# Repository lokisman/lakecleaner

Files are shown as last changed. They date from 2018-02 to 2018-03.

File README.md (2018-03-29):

# Lake-Cleaner Bot

* Design of a Lake-Cleaner Bot.

====================================================================================

## Aim of project:
* The main task of this project is to clean the polluted water bodies with the help of a cleaning bot which is controlled wirelessly and can be made autonomous.
* The bot has to perform the functions of collecting the solid trash present in the water bodies like plastic bags, plastic bottles, small objects, etc. Further it should also be able to cut small plants and weeds growing on the water surface and also collect them in the trash pit. After this process, it should empty this trash into a disposable pit.

## CAD View
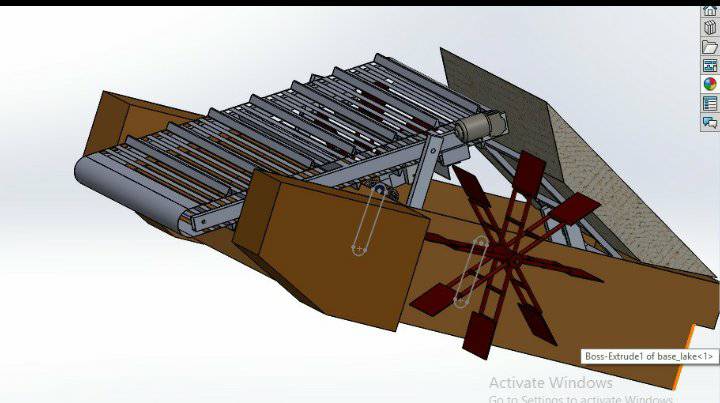
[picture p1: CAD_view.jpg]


====================================================================================

## Working principle:

### Conveyar mechanism
* This mechanism use for transfer waste,garbage from water body to dump box. The conveyer belt is mounted at an inclination to the chassis. As the cylinders over which the conveyer belt slides roll, the belt moves in the anti- clockwise direction so that the solid waste gets stuck in the projections made in the conveyer belt.

### Dumper Lifting Mechanism:
* It is use to lifting the box.
* In this lead screw mechanism is use. It gives us linear motion.
* Here, lead screw is mount on coupler.
* lead screw is mounted with motor shaft. So, when motor shaft is moved in anti-clockwise direction, due to linear motion dump box is move upward.

====================================================================================

## Different Parts:

### Chasis:       
* The chassis is designed so as to accommodate the wheels mountings, conveyer belt mechanism mounting, four link                            mechanism mounting and finally the chassis should sustain the weight of the (garbage + self-weight).

=====================================================================================

## Original Picture of Bot

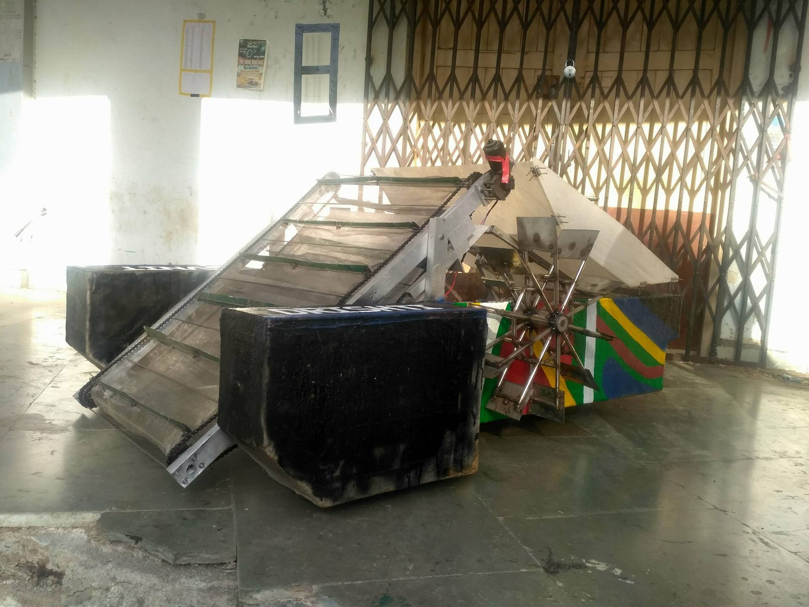
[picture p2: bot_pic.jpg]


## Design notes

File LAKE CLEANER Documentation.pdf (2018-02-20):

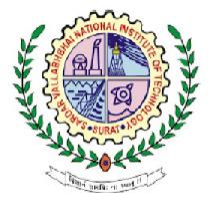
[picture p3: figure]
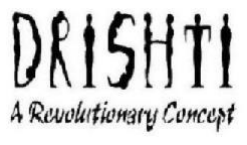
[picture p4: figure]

# _________________________ LAKE CLEANER

Project timeline spanned from 10th September,2017 to 15th February,2018
Team Members: | Mentors:
- | Parth Patel | Harshit Aghera
- Darshit Bhankar | Divya Poddar
- Darshan Wankhede | Sanjana Dhiran
- Lokesh Kumar Meena | Aparna Koduri
- Ranjeet Singh | Ankit Anand
- Yash Sharma | Kaishavi U.

# CONTENTS

1. Aim
2. Motivation
3. Working Mechanisms
a. Trash Collecting Mechanisms
b. Dumper Lifting Mechanisms
c. Chassis
d. Weed Cutting Mechanisms
4. Manufacturing
a. Chassis
b. Lead Screws
c. Wheels
d. Conveyer Belt
e. Body
f. Cutting Mechanism
5. Future Modifications
6. Result

# AIM OF THE PROJECT:

The main aim of the project is to clean the polluting water bodies with the help of a cleaning bot which is controlled wirelessly and further can be made autonomous.

The bot has to perform the functions of collecting the solid trash present in the water bodies like plastic bags,plastic bottles,small objects,etc… Further it should also be able to cut the small plants and weeds growing on the water surface and also collect them in the trash pit. After this process, it should empty this trash into a disposable pit.

# MOTIVATION:

Nowadays, a lot of manual labour is being is employed in the cleaning of the rivers, lake and other local water bodies. A large amount of time and money is wasted by the government in this task to reduce the river contamination.

Hence to provide a Technical Solution for a Time and Cost Effective method to reduce the manual labour, we thought of making an automatic bot which can efficiently do all the chores in less time. This is the basic motive behind our “River Cleaning Bot”.

## DESIGNING SOFTWARE USED:

## SolidWorks

## ANALYSIS SOFTWARE USED:

## Ansys

# WORKING PRINCIPLE:

The different mechanisms used in the different parts of the bot are as follows:

(A) Trash Collection Mechanisms:
(i) PNEUMATICS:
Pneumatics is a type of linear actuator which uses air pressure as the actuating force.
We thought of using the pneumatics to lift the collecting plates to a certain level and we would use four link mechanism to lift this whole assembly to dump this collected trash in our dumper container.
We made a SolidWorks Model for our mechanism and manufactured it.

Errors in the Mechanism:

1) The air pressure was not able to bear enough weight. Appropriate amount of the air pressure required was not being generated in the cylinders. This reduced the amount of garbage that the bot can carry at a time.
2) The air pressure in the cylinder would reduce at a faster rate. So while in operation, the cylinders will have to be refilled many times in quick succession. This will increase the cost of operation and also it is not feasible to again and again fill the cylinders.
3) We would have to install a pressure regulator to maintain the air pressure at a constant value.
So, we had to switch over to some other alternative mechanism.

(ii) CONVEYER BELT MECHANISM: This mechanism uses a Conveyer belt to collect the solid waste from the water body and transfer it to our dumper container. The conveyer belt is mounted at an inclination to the chassis. As the cylinders over which the conveyer belt slides roll, the belt moves in the anti- clockwise direction so that the solid waste gets stuck in the projections made in the conveyer belt. Just below the conveyer belt assembly is kept our dumper container. When the dumper is full, our four link mechanism lifts this dumper and disposes off trash out of the bot on the ground.

(B)Dumper Lifting Mechanisms:
(i) FOUR LINK MECHANISM:
We thought of various designs by the help of which we can lift the dumper upto such an elevation so that the trash can fall on the ground without any trash being left inside the dumper.

Our main aim was to give minimum rotation to the driver link and get maximum inclination of the dumper.

We finally arrived at the above design. Here the Inclination we get is the maximum.

(ii) LEAD SCREW MECHANISM: We are using a lead screw arrangement for the lifting of the dumper. The lead screw arrangement works as a linear actuator in our case. We mount the lead screw onto the chassis of the bot. The nut traverses on the lead screw and pushes the dumper along with it. So basically, there is one fixed link, two movable links and a lead screw. This completes our mechanism for the lifting of dumper container.

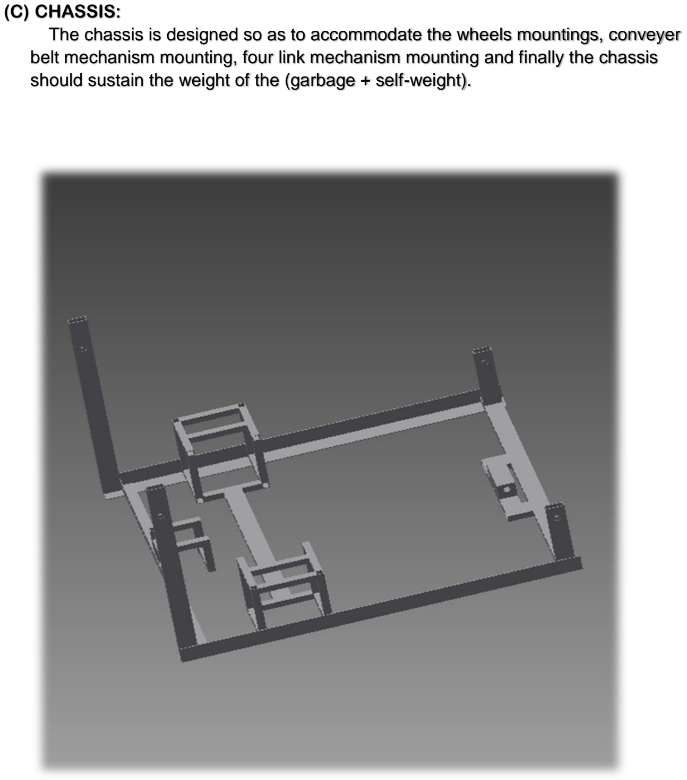
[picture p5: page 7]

(C) CHASSIS:
The chassis is designed so as to accommodate the wheels mountings, conveyer belt mechanism mounting, four link mechanism mounting and finally the chassis should sustain the weight of the (garbage + self-weight).

(D) WEED CUTTING MECHANISM:
We thought about two types of cutting/ shearing mechanisms which are :
(i) Reciprocating Type Cutter

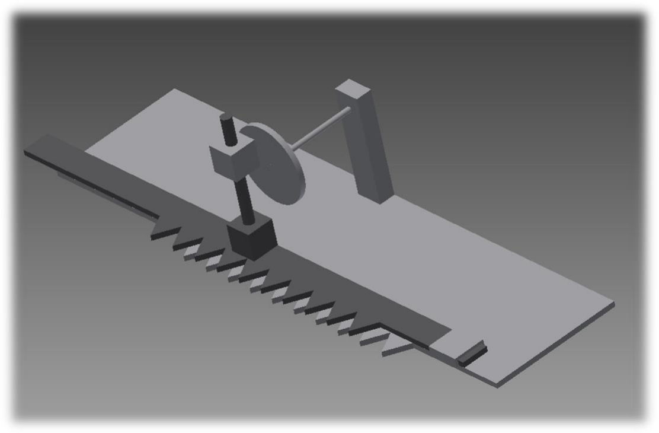
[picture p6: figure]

(ii) | Rotating Type Cutter
| In which the cutter roates and cuts the plants. The whole assembly is mounted on the arm which will have three degrees of freedom. By use of the arm we can adjust the depth of the cutter inside the water so that the cutting can be done at different depth.

# CAD DESIGNS:

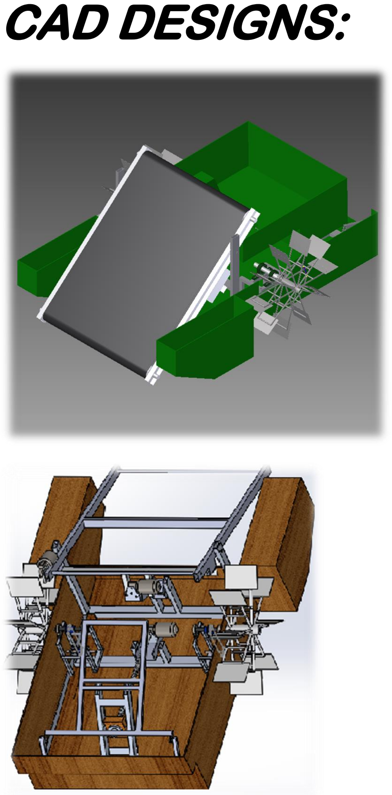
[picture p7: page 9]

# MANUFACTURING:

## Materials Used:

- Aluminium Sheets, Aluminium Box Sections
- Teak Wood
- Plywood
- FRP(For Body)
- Stainless Steel(For Propellers)

## Motors Used:

- Viper Motors (100 kgcm , 50 rpm)

## CHASSIS:

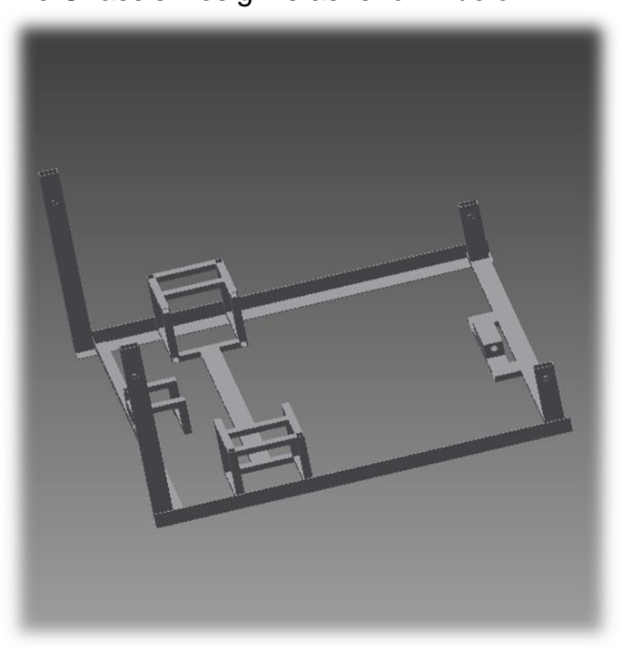
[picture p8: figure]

The Chassis Design is as shown below:

## LEAD SCREWS:

The motor mountings for the Lead Screws were manufactured with aluminium. Two of these were made. One for the garbage dumper and other for the adjustment of the inclination of the conveyer belt in the water.
The pillars for the hinging of the lead screw were also made and fixed exactly at the center of the middle link.

The problems faced with this was that:-
- The lead screw was wobbling very much even after properly connecting the coupler. We made the whole motor mounting twice but still the lead screw was wobbling about its axis. Due to this, the lead screw could not properly propagate on the nut and whole assembly was encountering jerks again and again. After checking each and every component in the mounting, we finally found that the coupler was not perfect. The holes which were connecting the lead screw with the coupler were not straight. Hence we made new holes and thus the problem was solved.
- The holes in the two pillars for hinging had to be exactly co-axial.

- The extension of the lead screw was hitting the bot as it was progressing further. Also the height of hinging was decided on the factor that the extension of the screw should not hit the bot. We had to cut some portion of the screw to reduce its length.

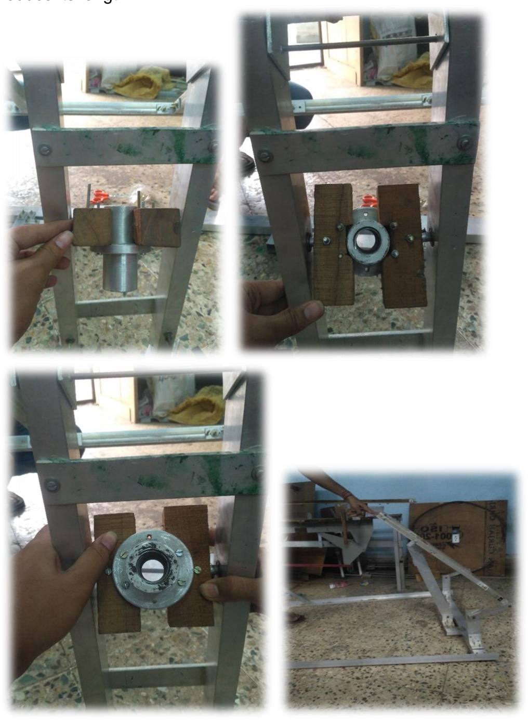
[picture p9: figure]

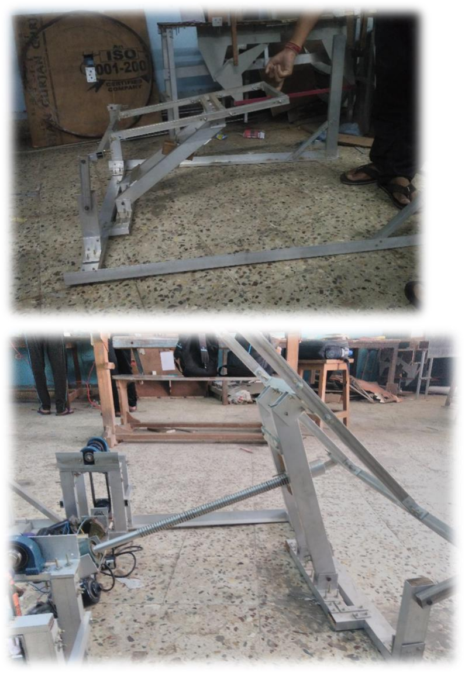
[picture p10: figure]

## WHEELS:

We cut cylindrical hollow rods of lengths 95cms and 230cms from long steel rods. Also 20 aluminium plates were cut. These were welded in the desired orientation to make the wheels which were finally coupled with the motor to make things work. The shape of the wheels is shown below.
We welded the wheels by Electric Arc Welding Machine.
The motor was mounted on the base of the bot itself because it would be difficult to mount the motor in air as then the clamp would have to bear high load to hold it. The motor was connected to a pulley which would transfer the power to the axis of the wheel through a belt-drive pulley system.
The problems faced with this was that:-
- The frame for the assembly of the wheels with the bot was to be made very precisely such that that the two parts should be paralle to eah other otherwise the axis would not be exactly straight. Hence we had to fix this frame by taking proper measurements from both sides.
- This required very much trial and error as we had to decide the distance between the wheel axis and motor axis such that the pulley belt would neither be very much tight nor be loose. For this we had to provide supports of 12mm and 8mm plywoods at the base.
- The pedestal bearings were fitted on the top of the frame from which the axis of the wheel would pass. These bearings should be exactly collinear and axial otherwise the wheel motor would have to bear much load and the axis of the wheels may break.
- The small bearings were to be fitted in the clamps through which the motor axis were to pass. We had a hole saw of 30mm and the bearings were of 31.5mm. So we had to enlarge the hole by drill machine or file in order to fit the bearings. This task took very long as we had to do this four times.
- We also had to make a Jig as per our wheels dimensions so that we could do welding easily and in proper orientation. We had to maintain a very low current of 33A to do the welding as the S.S. would melt at higher current. The welding took about 3-4 days.

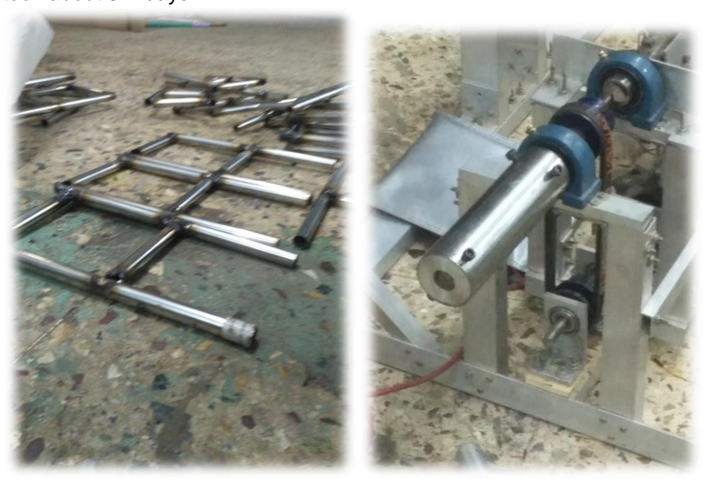
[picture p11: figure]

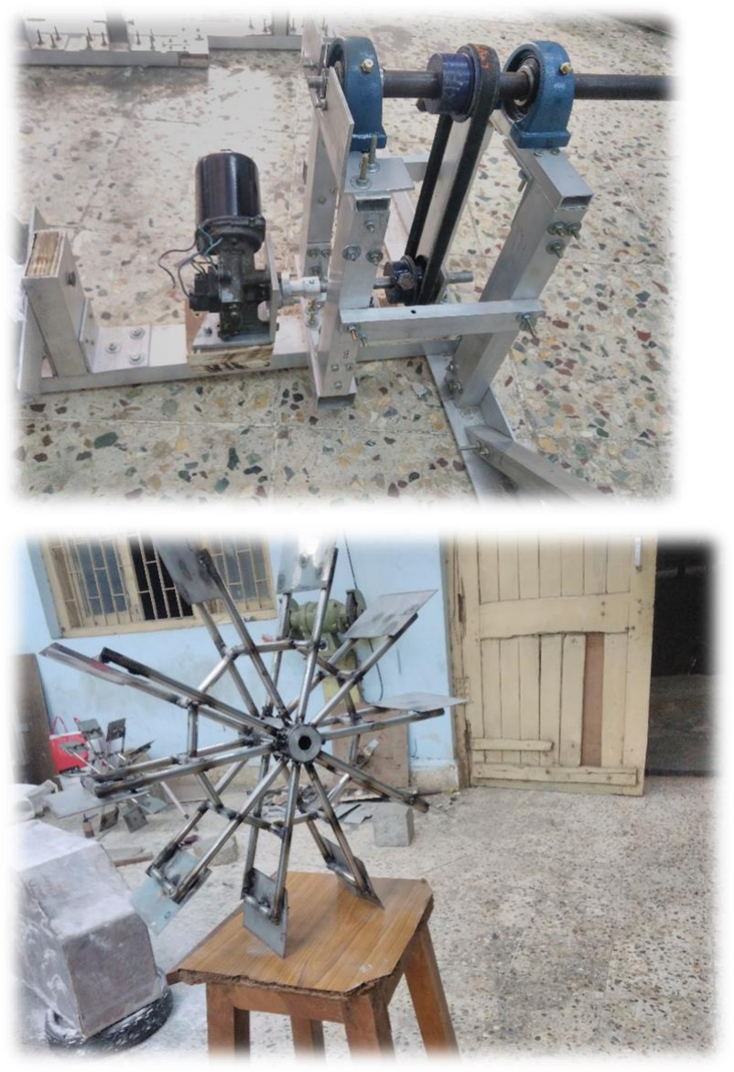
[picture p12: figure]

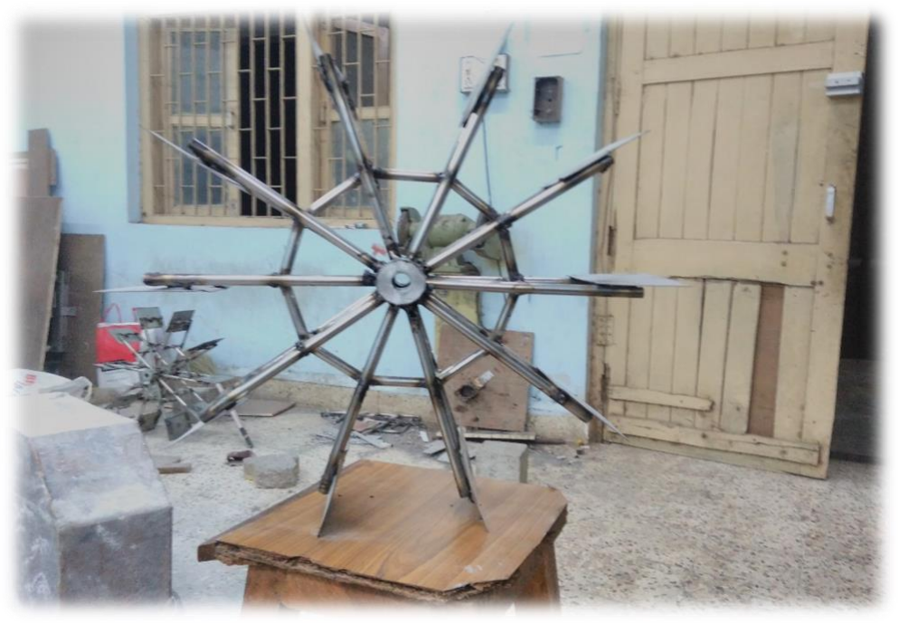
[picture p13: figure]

## CONVEYER BELT:

The design of the Conveyer belt assembly is shown below.

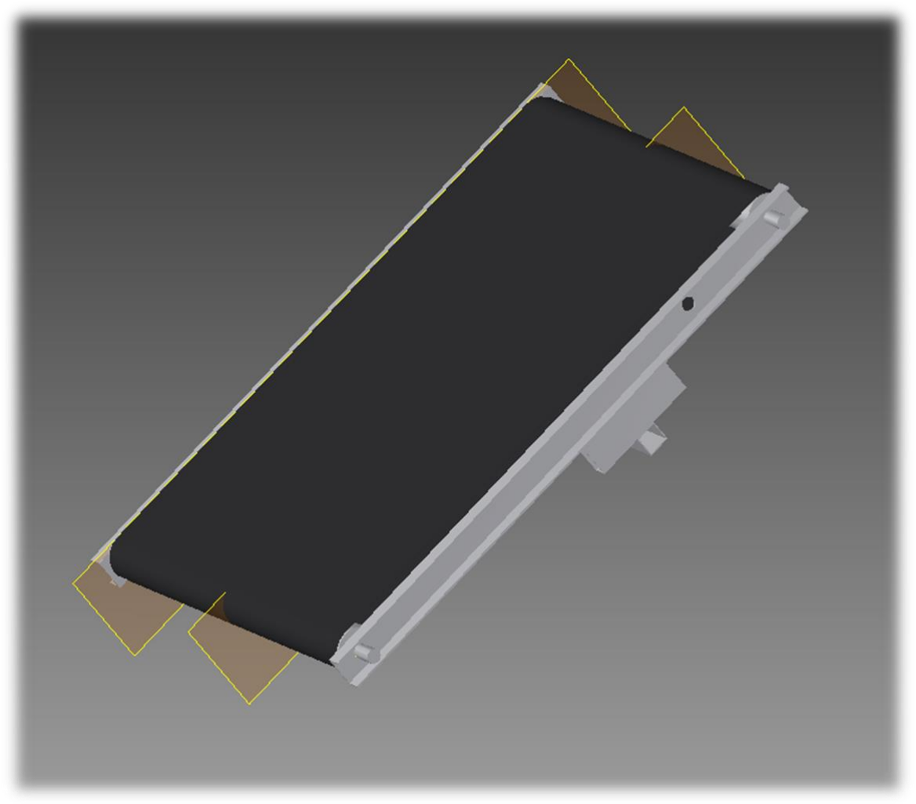
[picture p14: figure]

The frame over which the conveyer belt would be placed was made from aluminium box sections. Here also co-axial holes were made to hinge this.

The conveyer belt is made up of a wire mesh so that while collecting the garbage, water which also will come up will be drained through this mesh and only garbage will be transported to the dumper.

The wire mesh would be laid over a frame made by the chain of bicycle and rim spokes which we had made. This would run over four (two on each side) sprockets (free-wheels used in bicycles over which the chain runs over).Now we had to also think about how to complete this assembly.

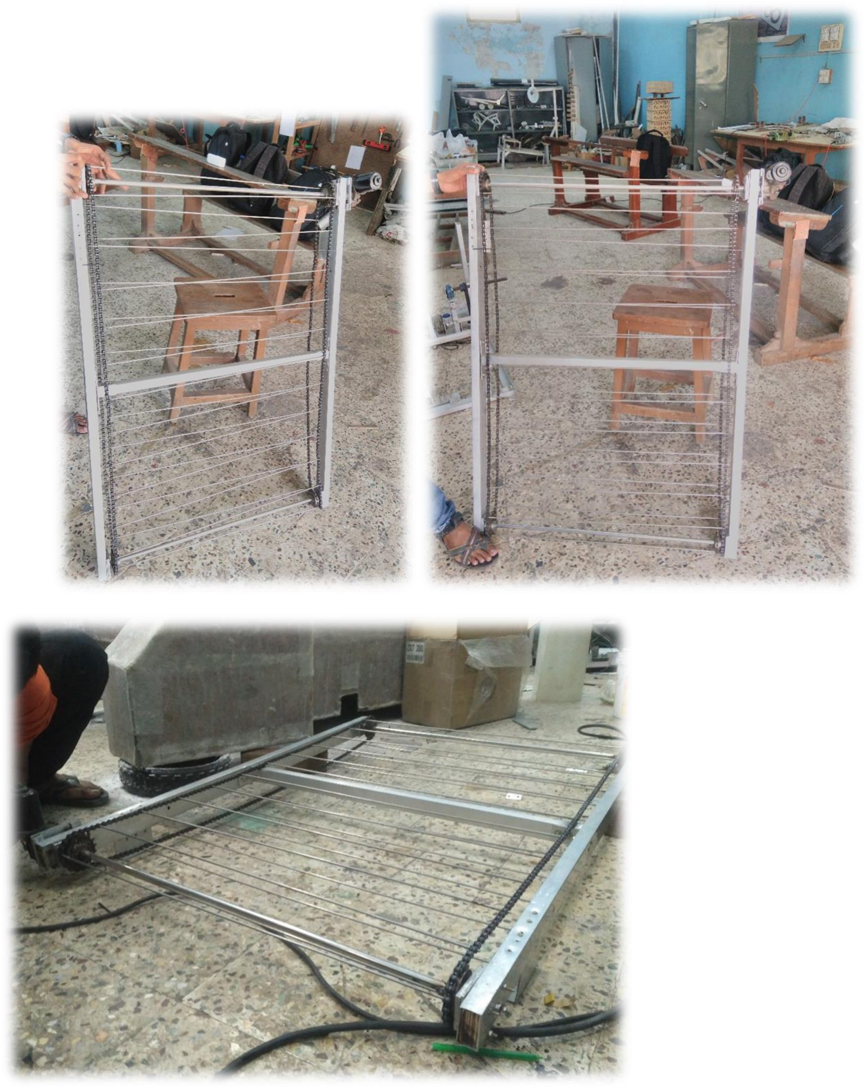
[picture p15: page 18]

The problems faced with this was that:-

- The mounting of the motor required for the motion of the conveyer belt was difficult as it would at some elevation from the base of the bot at some height in air. We finally thought of a way to make a strong base for the motor by inserting multiple plates outside the box section at the location where motor was to be mounted. Thus the strength of the part became considerably good and the overall thickness of the section was also increased. Hence the motor could easily be mounted such that the coupler was also accommodated.
- The chain assembly posed a very big problem. Upon testing we found that the the chain would frequently disengage from the sprocket and thus would stop the the movement of chain. So we adjusted the distance between the left and right chain assembly and also made sure that the two individual chain assemblies are parallel to each other. We also welded the sprockets to the shaft at the proper distance.
- The small bearings were to be fitted in the plates through which the motor axis were to pass. We had a hole saw of 30mm and the bearings were of 31.5mm. So we had to enlarge the hole by drill machine or file in order to fit the bearings. This task took very long as we had to do this four times.

We made a video of the conveyer belt testing. The link is given below:

https://drive.google.com/open?id=1fzCtKUJaTC_JY0II-J_MTXBbZ5uP1NqD

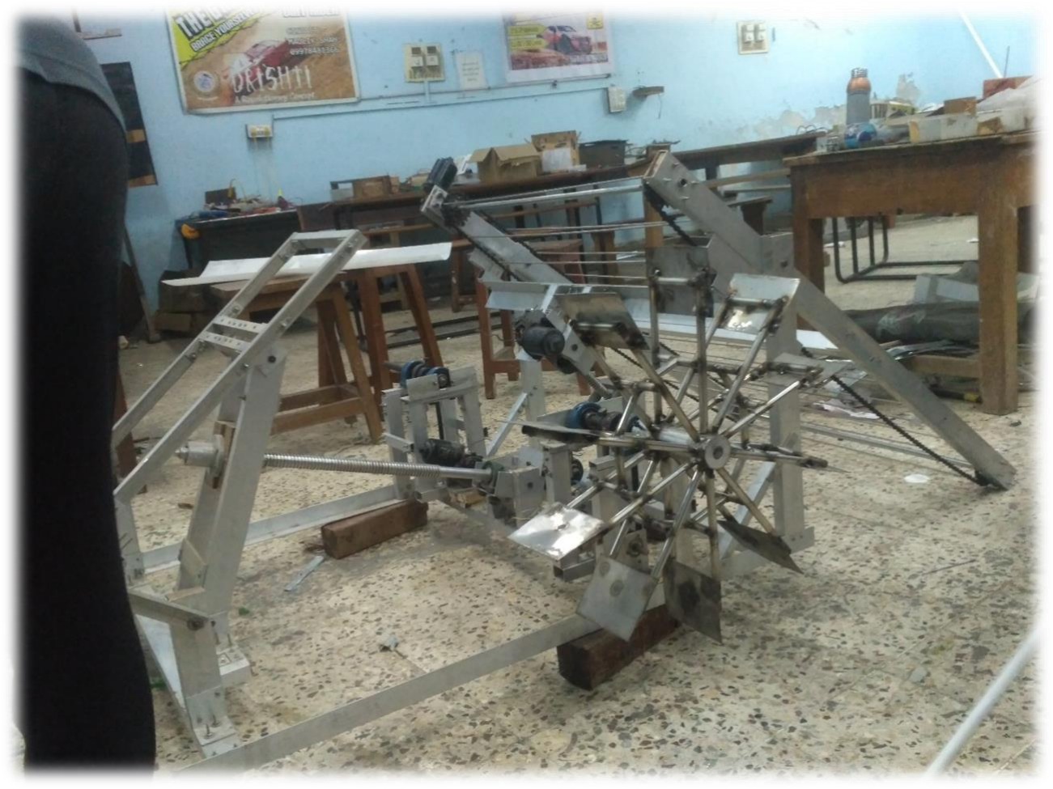
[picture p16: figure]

## BODY:

We made the body of the whole bot inside which the bot will be placed to protect it from water.
We made this box from plywood and then coated it with FRP (Fibre Reinforced Plastic). The purpose of using the FRP was to insulate the plywood from water and provide the strength to the structure. The CAD model as well as the actual prepared part is shown below in the figure.

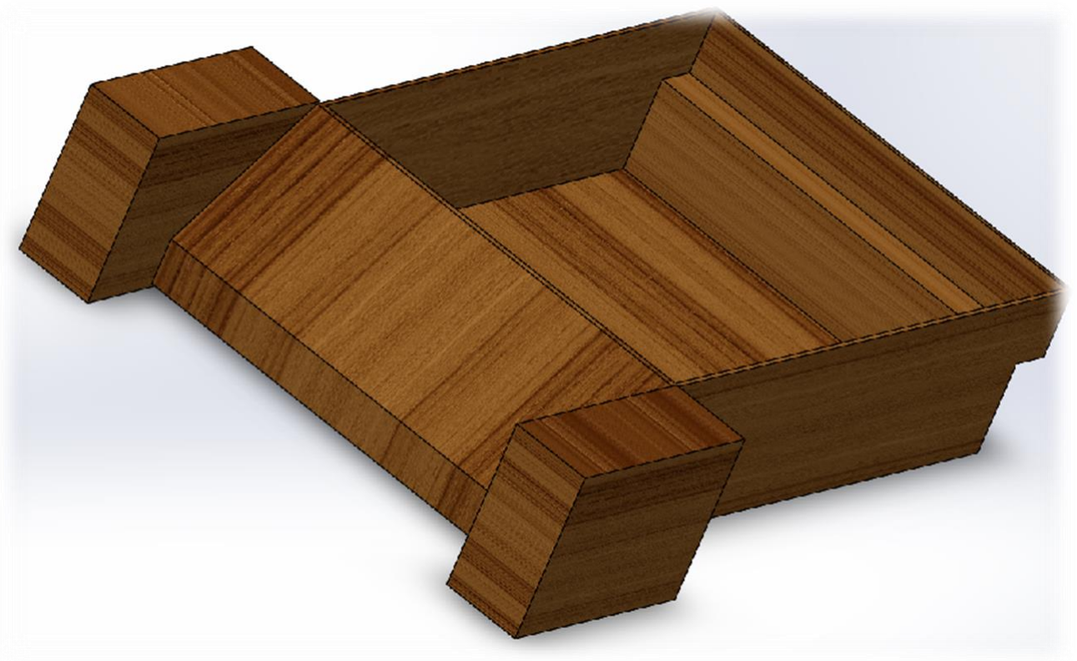
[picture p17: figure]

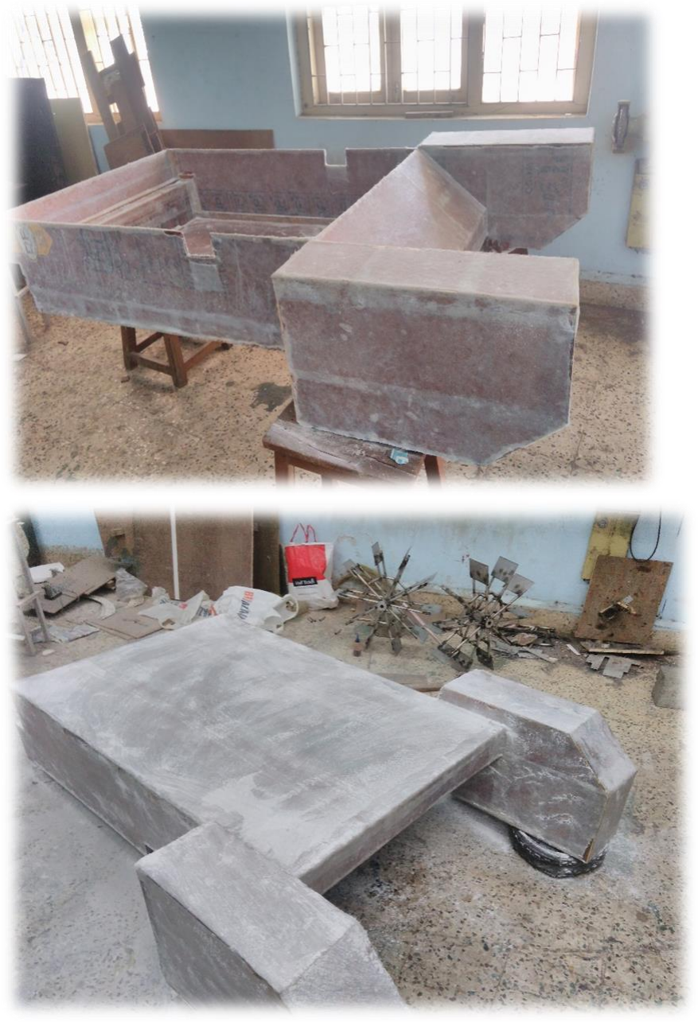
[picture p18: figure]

We had to provide two separate structures as you can see at the front part of the bot. The C.G. of our bot was coming out to be at the front side of the bot. These were made hollow from inside and the main purpose of these were to provide buoyancy to the bot to keep it from drowning from the front portion.

We had to provide two coatings of FRP on the edges so as to seal the edges completely and prevent entry of water into the bot.

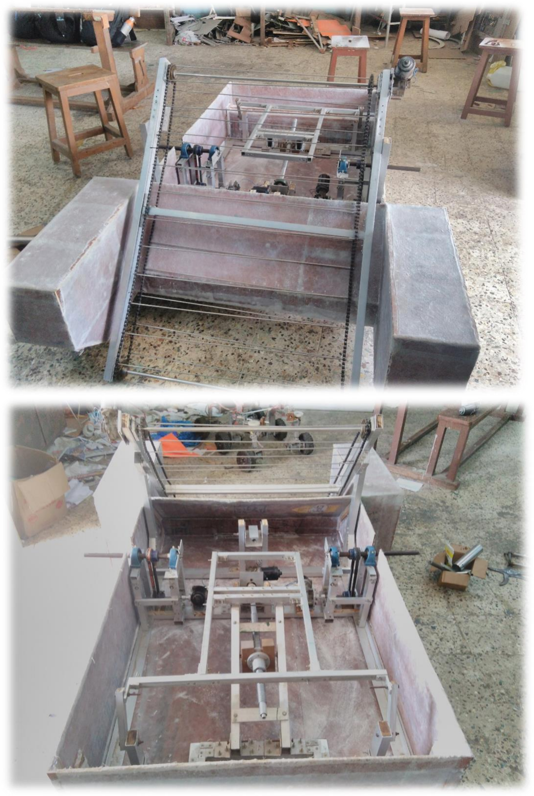
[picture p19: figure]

## CUTTING MECHANISM:

After thinking about both the designs of the cutter – rotating type and reciprocating type ; we made prototypes of both types with tin sheets and plywood. We tested them and came to the conclusion that rotating type is more suitable. Ther ewer reasons to believe so:

1) For the same rpm of the motor, we could get more efficiency from the rotating type cutter.
2) The shearing effect was more prominent in the rotating type.

So, we made the blades for the cutter from thick steel plates in the desired shapes.

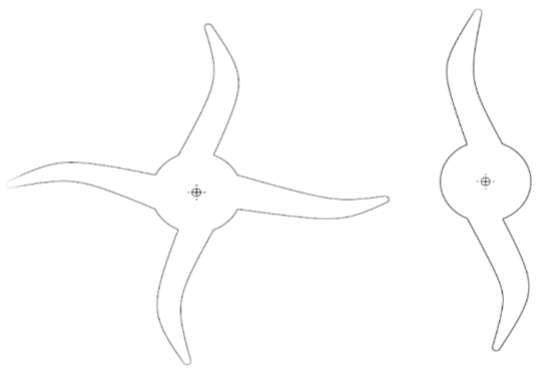
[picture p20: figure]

After cutting we sharpened their edges so that they would cut more easily at high speeds. Then we polished their surfaces by the help of grinding blade. The finally prepared blades are in the figure shown below.

# FINAL BOT:

# FUTURE MODIFICATIONS:

- We can also devise a mechanism to remove oil and dirt from the water which can help stabilize the ecosystem of the aquatic lives.

- To be able to distinguish between obstacles and boundaries and the garbage the robot has to clean and pick up.
- To be able to execute driving successfully on water surface.

# RESULT:

The bot was working properly.

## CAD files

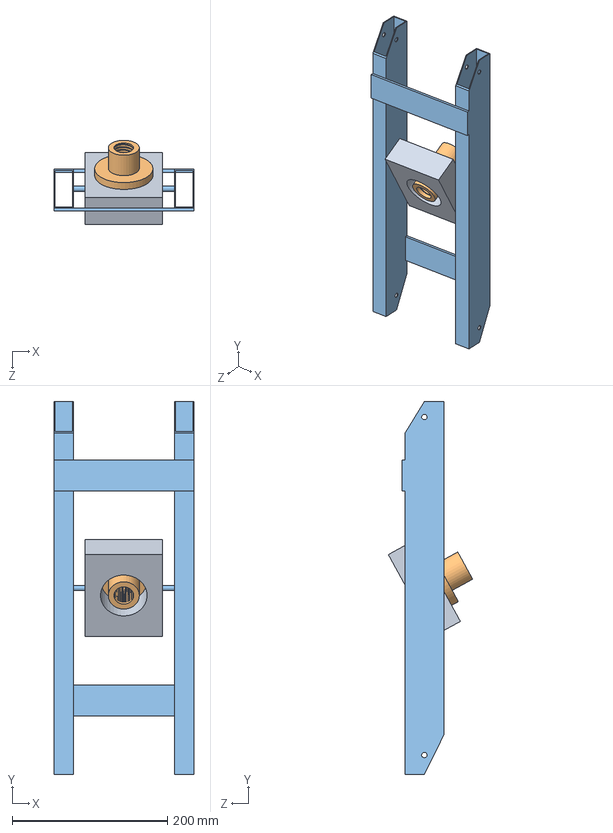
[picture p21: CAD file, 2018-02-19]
LAKEASSEMBLY-1.SLDASM
180.0 x 480.0 x 108.6 mm
wodenpart lake
lakebase3
laKebase2

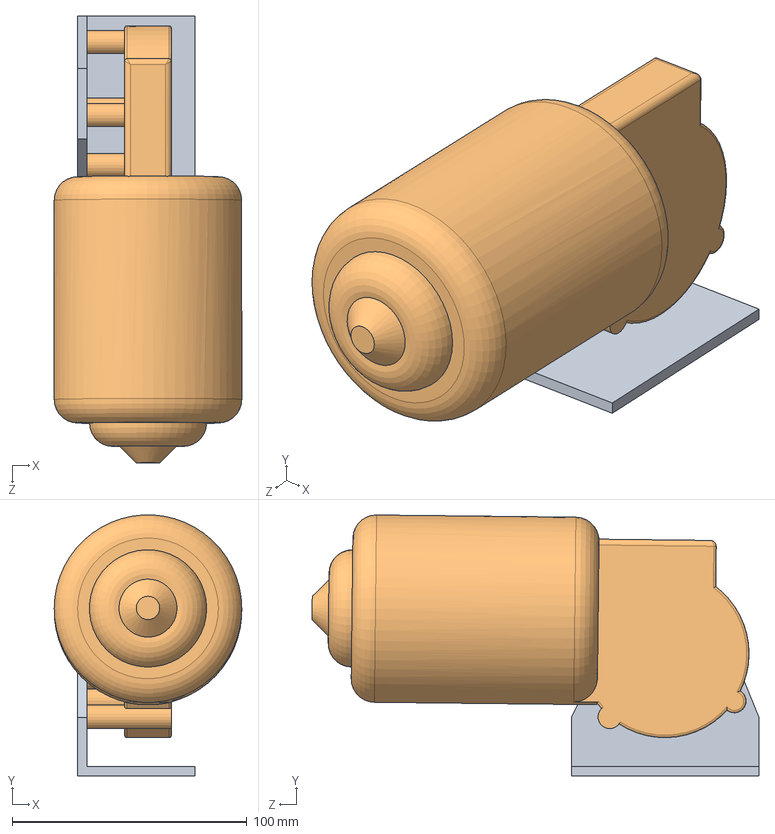
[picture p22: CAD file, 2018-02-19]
motor_assem.SLDASM
80.0 x 111.3 x 190.6 mm
l_part_conveyar
LAKE_MOTOR

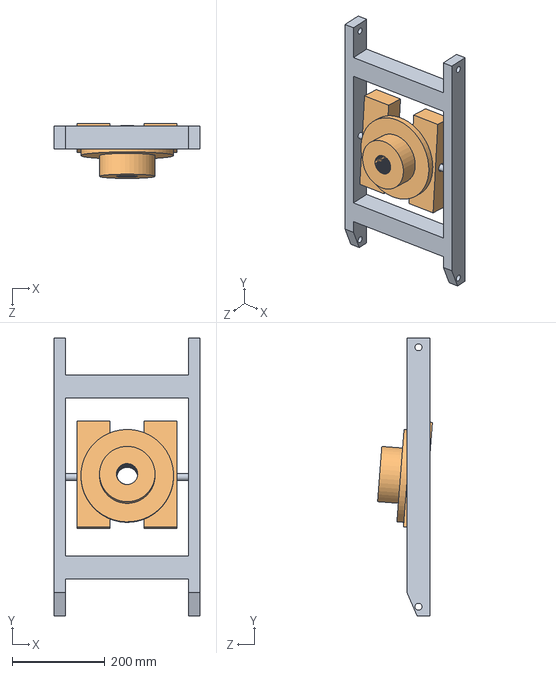
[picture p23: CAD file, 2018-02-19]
LAKEASS-1.SLDASM
315.0 x 600.0 x 118.6 mm
LAKE-1
LAKE-2

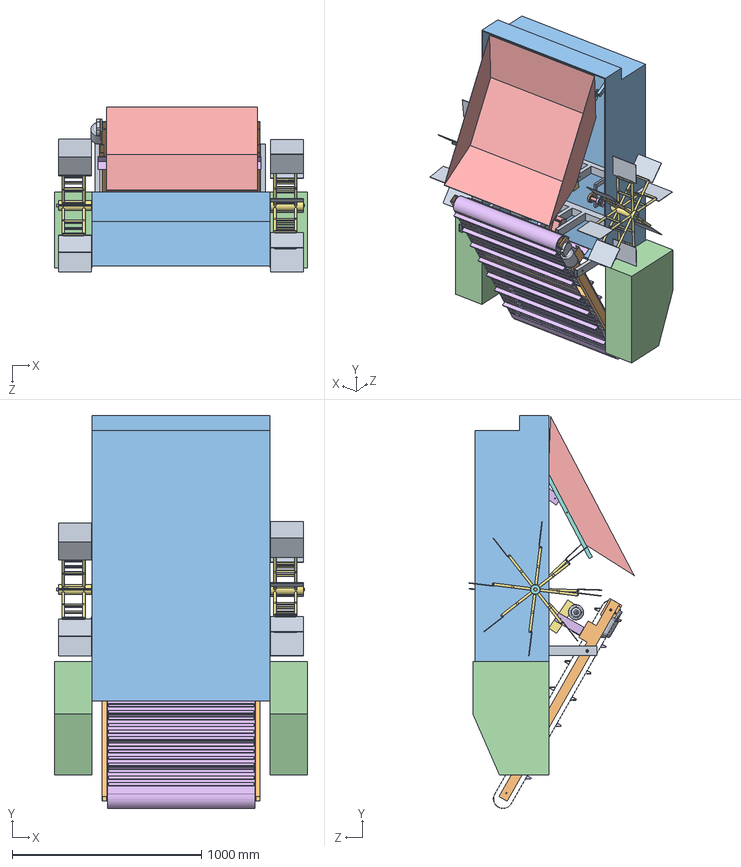
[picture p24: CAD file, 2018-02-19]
LASE.SLDASM
1340.0 x 2078.0 x 874.7 mm
LAKE-BASE
lake-base2
LAKE x 2
wodenpart lake
lakebase3
laKebase2
LAKE1
LAKE_BASE_STAND
radial ball 2 x 4
LAKE_BEARING x 4
LOWER_PART_PULLYS_ROD x 2
FINAL_BEARING x 4
UPPER_PART_PULLYS_ROD x 2
BASE_PULLYS x 4
FINAL_WATER_WHEEL x 2
COUPLER x 4
WHEEL_PLATE x 16
conveyer_lake
CONVEYAR ROD x 2
lead_screw
conveyar_motor_coupler
conveyar_upper-part
conveyar_coupler x 2
l_part_conveyar x 2
LAKE_MOTOR x 3
conveyar_single_motor_plate
base_lake
front_part x 2
final_dump_box
LAST-CONEYAR

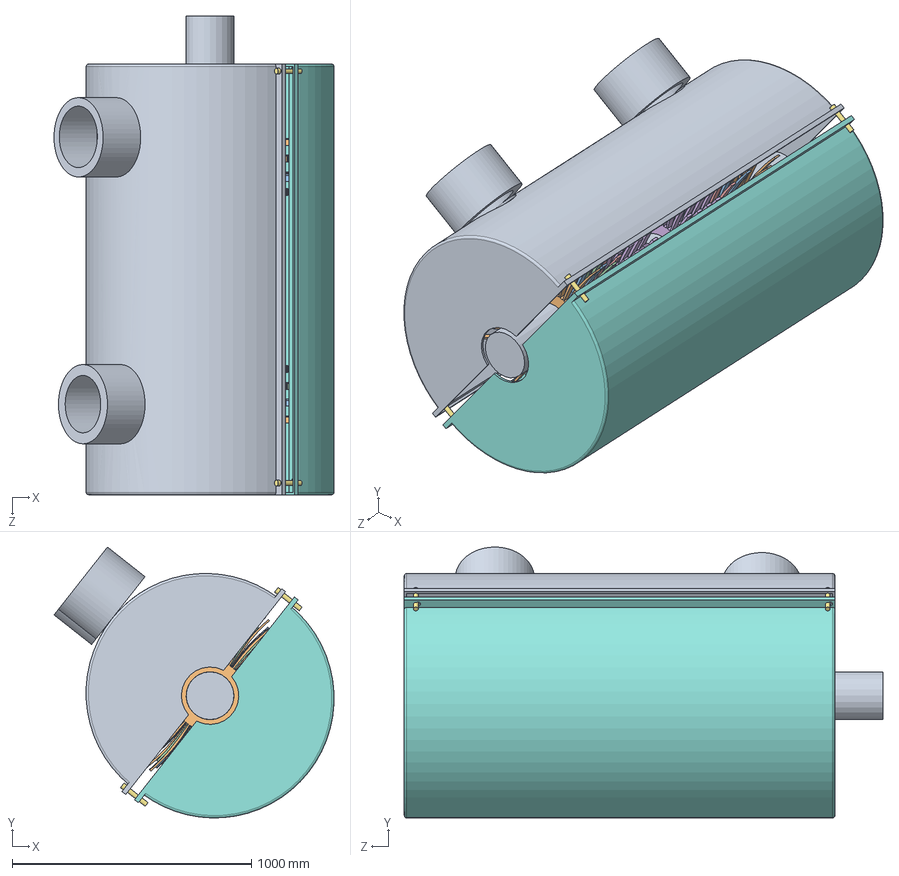
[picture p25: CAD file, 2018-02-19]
turbineassem_1.SLDASM
1170.2 x 1132.1 x 2000.0 mm
turbine_rod
low pressure turbine plate.SLDPRT_1 x 3
low pressure turbine plate.SLDPRT_1 - Copy x 2
low pressure turbine plate.SLDPRT_1 - Copy (2) x 2
low pressure turbine plate.SLDPRT_1 - Copy (3) x 2
low pressure turbine plate.SLDPRT_1 - Copy (5) x 10
bolt_2 x 4
turbinne_part
turbinne_part - Copy

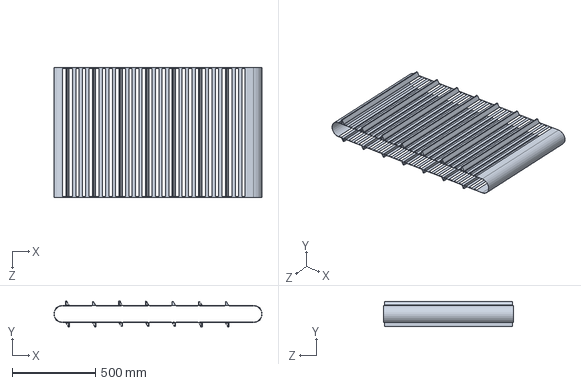
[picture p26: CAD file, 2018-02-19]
LAST-CONEYAR.SLDPRT
1252.0 x 152.0 x 780.0 mm

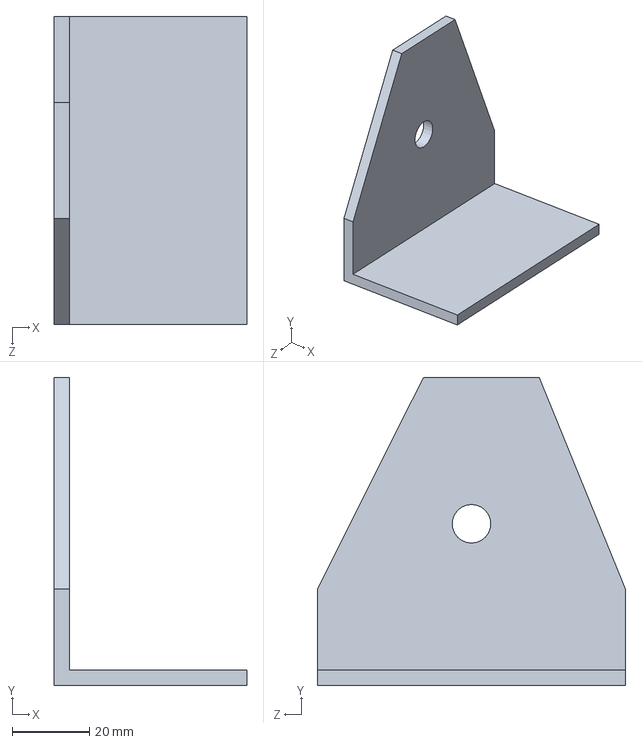
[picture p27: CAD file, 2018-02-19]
l_part_conveyar.SLDPRT
50.0 x 80.0 x 80.0 mm

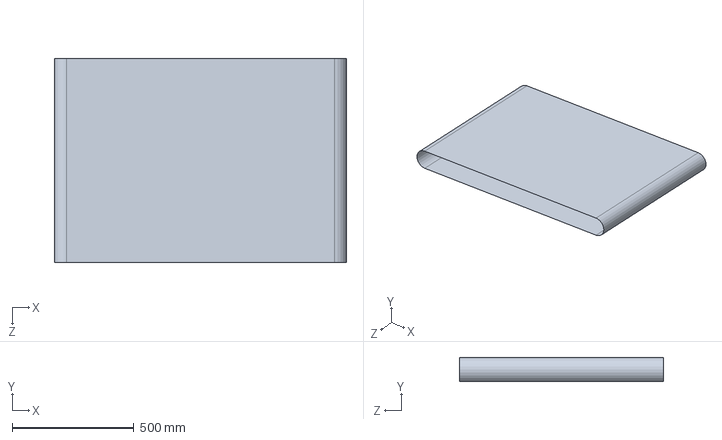
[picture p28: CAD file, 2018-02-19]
LAKE-BELT.SLDPRT
1200.0 x 100.0 x 840.0 mm

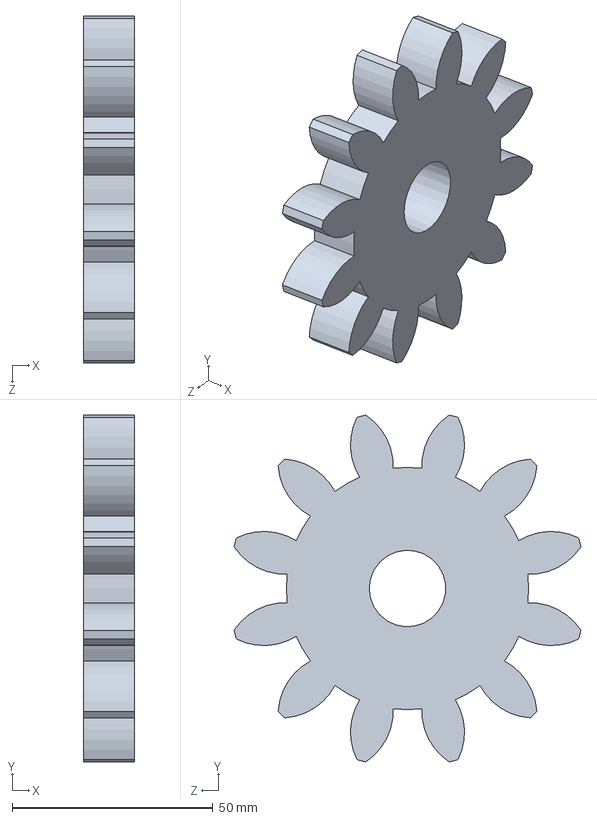
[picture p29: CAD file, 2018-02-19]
SPUR_GEAR.SLDPRT
12.7 x 86.4 x 86.4 mm

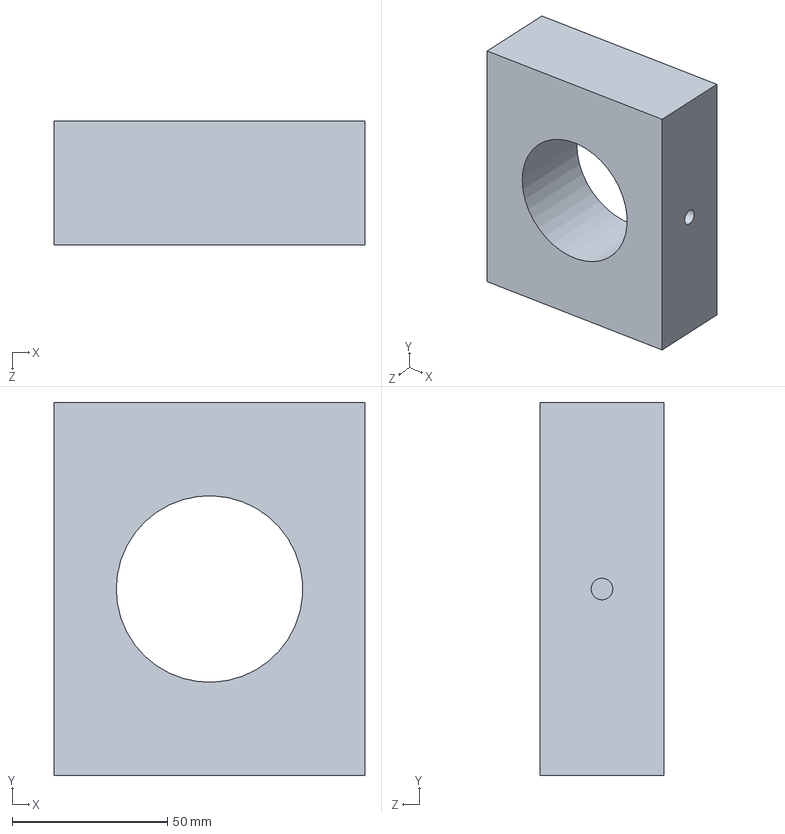
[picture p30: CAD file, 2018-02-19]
wodenpart lake.SLDPRT
100.0 x 120.0 x 40.0 mm

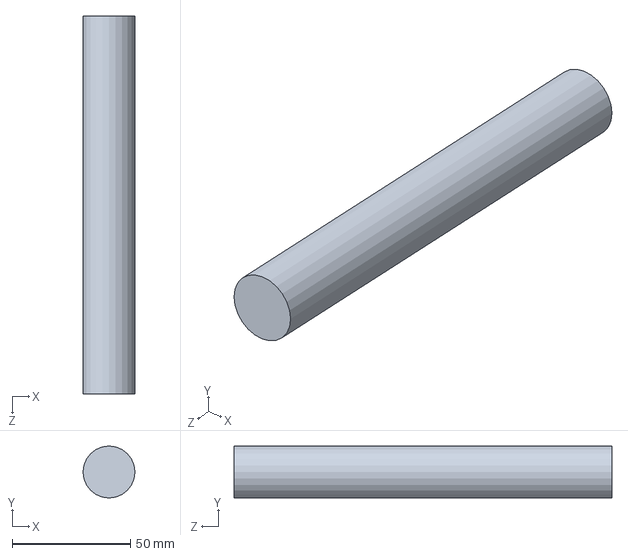
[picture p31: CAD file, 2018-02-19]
LAKE-12(SHAFT_PULLYS).SLDPRT
22.0 x 22.0 x 160.0 mm

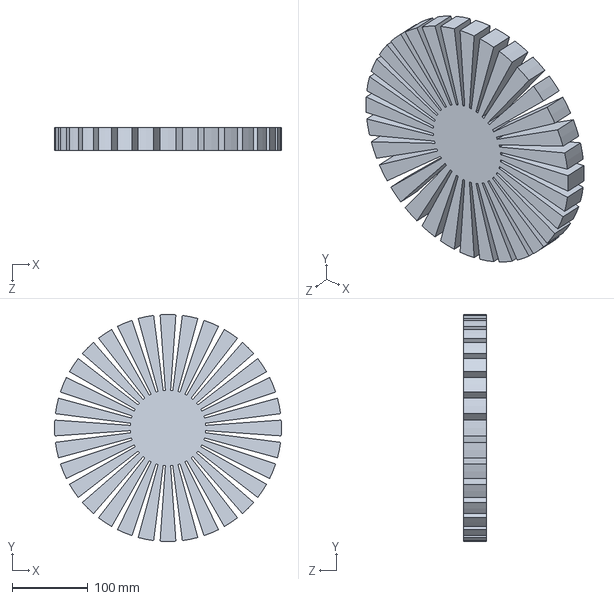
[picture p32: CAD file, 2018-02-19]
turbine_1.SLDPRT
300.0 x 300.0 x 30.0 mm

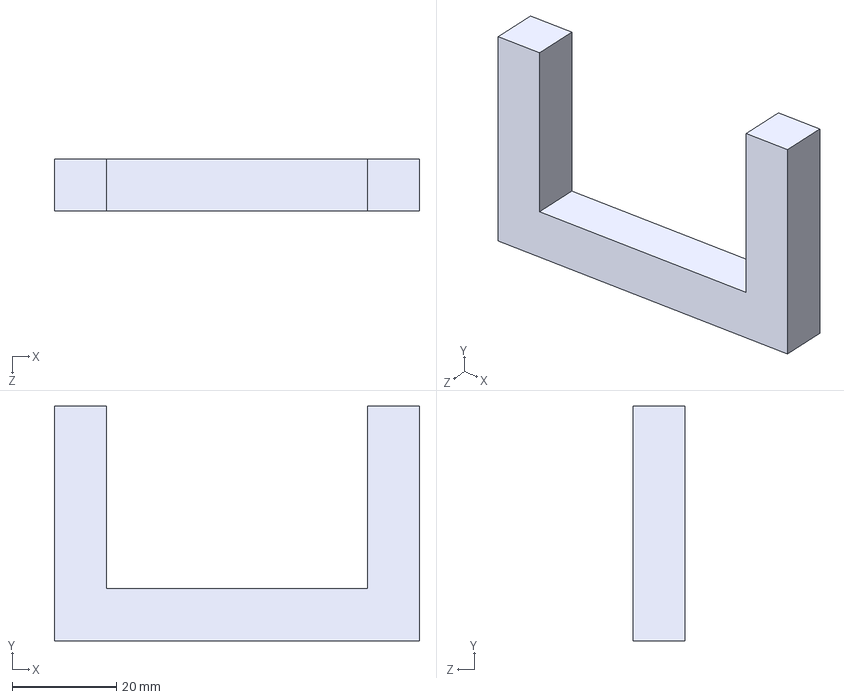
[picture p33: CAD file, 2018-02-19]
practise.STEP
70.0 x 45.0 x 10.0 mm

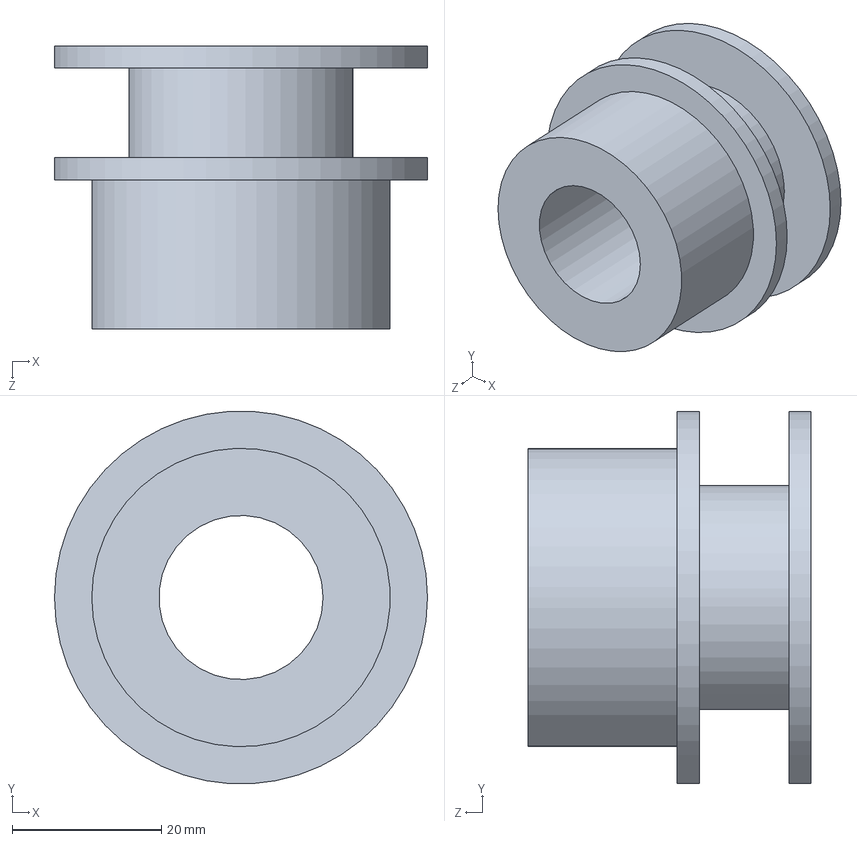
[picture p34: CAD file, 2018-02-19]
LAKE-11.SLDPRT
50.0 x 49.9 x 38.0 mm

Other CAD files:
LAKEASSEMBLY.SLDASM
wooden lake part.SLDPRT
higher pressure turbine plate.SLDPRT_2.SLDPRT
turbine_rod.SLDPRT
I beam.SLDPRT
LAKE-1.SLDPRT
LAKE-10.SLDPRT
LAKE-13.SLDPRT
LAKE-2.SLDPRT
LAKE-3.SLDPRT
LAKE-4.SLDPRT
LAKE-5.SLDPRT
LAKE-6.SLDPRT
LAKE-7.SLDPRT
LAKE-8.SLDPRT
LAKE-9.SLDPRT
LAKE-BASE.SLDPRT
LAKE-BEARING.SLDPRT
LAKE-BELT _ROD.SLDPRT
LAKE-WHEEL.SLDPRT
LAKE.SLDPRT
LAKE1.SLDPRT
LAKE6.SLDPRT
LAKE_4.SLDPRT
LAKE_BASE_STAND.SLDPRT
LAKE_BEARING.SLDPRT
LAKE_MOTOR.SLDPRT
LAKE_MOTOR_FINAL.SLDPRT
LAKE_OBSTAKLE PART.SLDPRT
LAKE_ROD.SLDPRT
LASE.x_t
LOWER_PART_PULLYS_ROD.SLDPRT
Lake-Y.x_t
Part1.SLDPRT
Part1.x_t
Part2.SLDPRT
Part3.SLDPRT
TURBIN_2.SLDPRT
UPPER_PART_PULLYS_ROD.SLDPRT
U_SHAPEAssem1.x_t
final_conveyar_last.SLDPRT
final_dump_box.SLDPRT
front_part.SLDPRT
higher pressure turbine plate - Copy (2).SLDPRT
higher pressure turbine plate - Copy (3).SLDPRT
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

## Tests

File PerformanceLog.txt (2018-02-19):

Mesh Preparation:  0 hr 0 min 2 sec
Standard solid mesh assembly imprint:  0 hr 0 min 0 sec
Standard solid mesh bolt head imprint and hard point processing:  0 hr 0 min 0 sec
Standard solid mesh total preparation including imprint:  0 hr 8 min 21 sec
Standard solid mesh total:  0 hr 8 min 26 sec
Beam mesh:  0 hr 0 min 0 sec
Mesh Preparation:  0 hr 0 min 2 sec
Standard solid mesh assembly imprint:  0 hr 0 min 0 sec
Standard solid mesh bolt head imprint and hard point processing:  0 hr 0 min 0 sec
Standard solid mesh total preparation including imprint:  0 hr 8 min 15 sec
Standard surface meshing for Solid Mesh:  0 hr 18 min 41 sec
Standard volume meshing for Solid Mesh:  0 hr 2 min 42 sec
Standard solid mesh arranging data:  0 hr 0 min 1 sec
Standard solid mesh total:  0 hr 26 min 57 sec
Beam mesh:  0 hr 0 min 0 sec

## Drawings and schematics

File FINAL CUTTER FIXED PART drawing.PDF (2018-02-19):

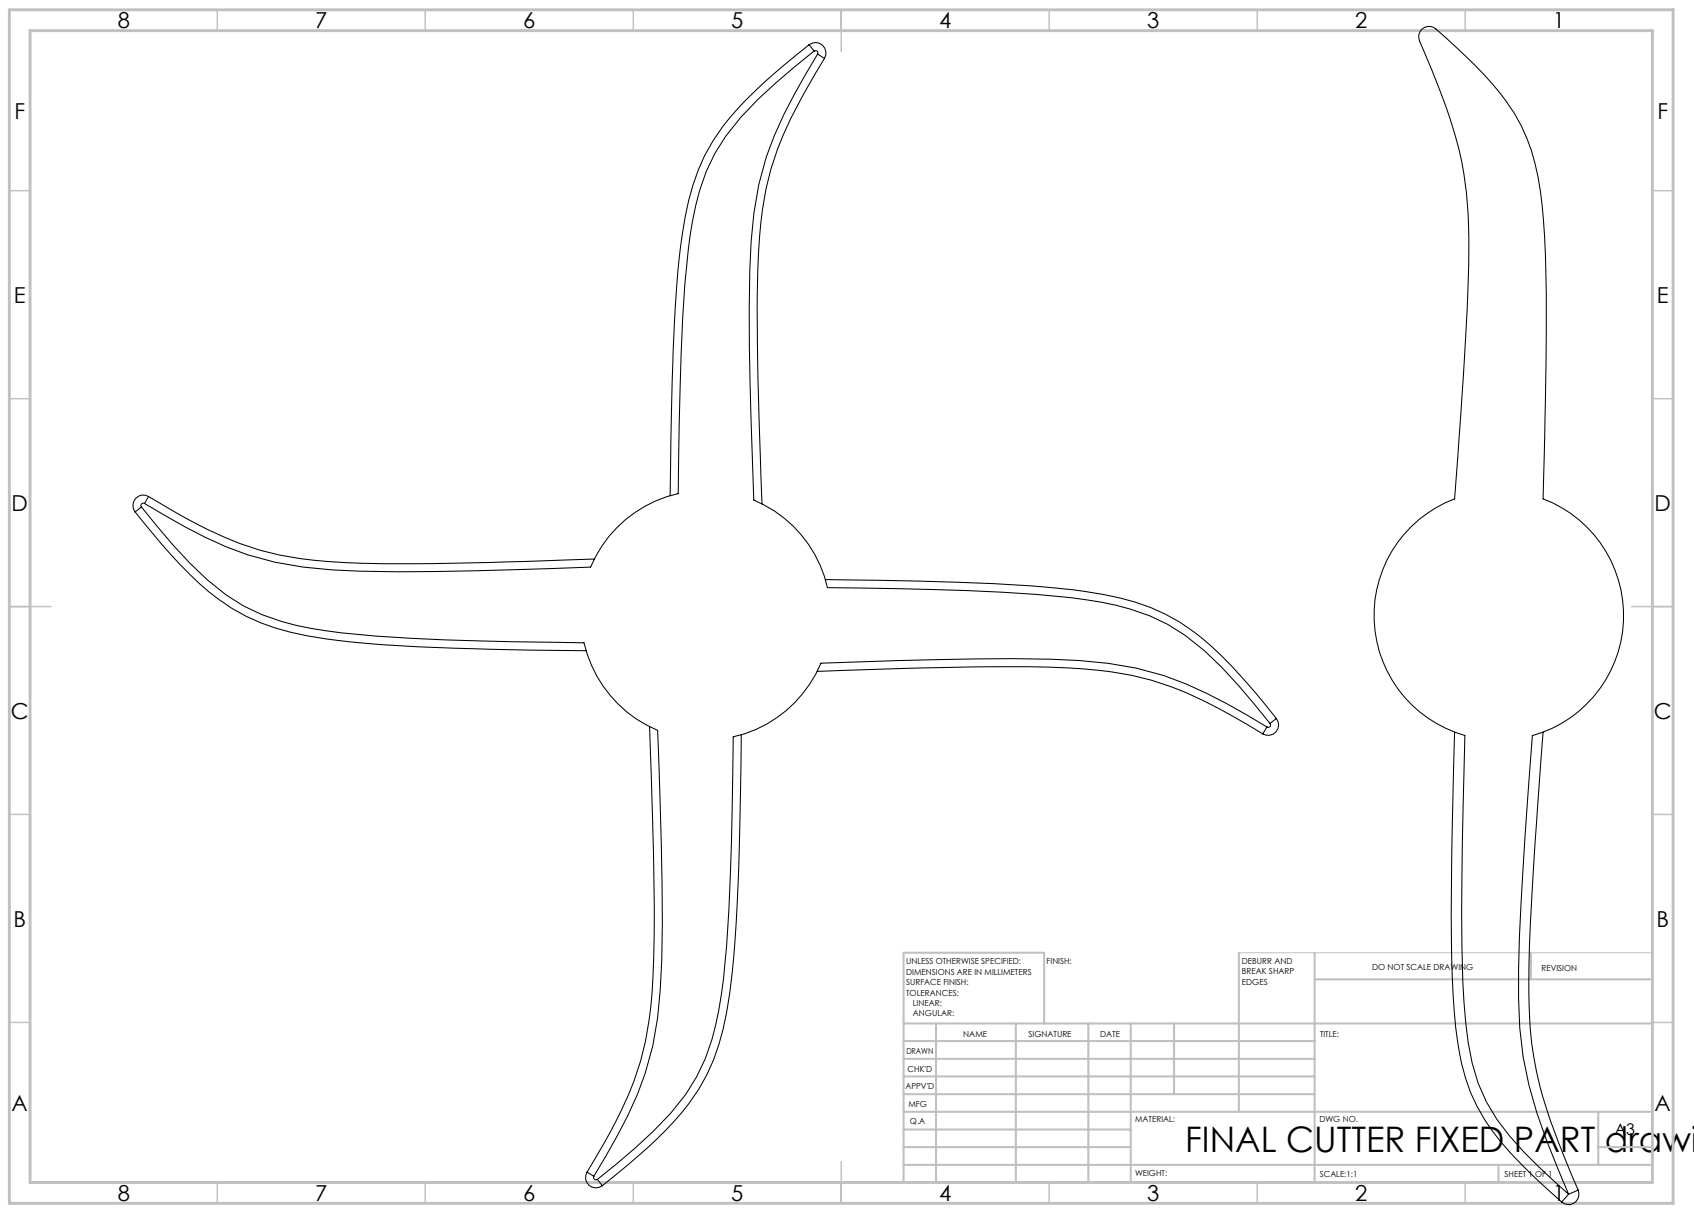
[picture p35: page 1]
FINISH:; DEBURR AND; BREAK SHARP; DO NOT SCALE DRAWING; REVISION; SCALE:1:1; SHEET 1 OF 1

UNLESS OTHERWISE SPECIFIED:
DIMENSIONS ARE IN MILLIMETERS
SURFACE FINISH:
TOLERANCES:
LINEAR:
ANGULAR:

NAME | SIGNATURE | DATE | | | | TITLE:

DRAWN
CHK'D
APPV'D
MFG
Q.A | | | | MATERIAL: | DWG NO. | A3

FINAL CUTTER FIXED PART drawing
